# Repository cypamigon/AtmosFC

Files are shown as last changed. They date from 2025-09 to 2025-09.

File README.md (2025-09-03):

# AtmosFC

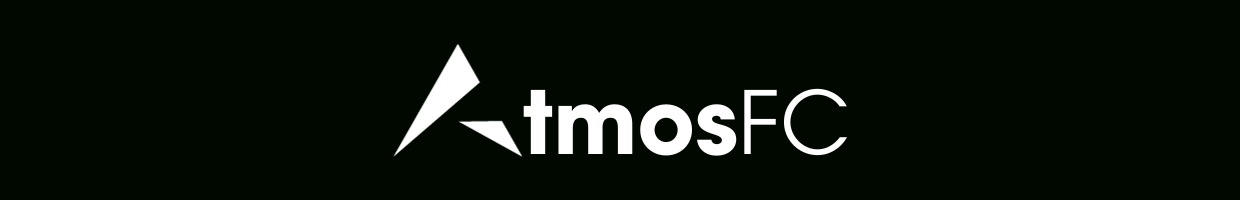
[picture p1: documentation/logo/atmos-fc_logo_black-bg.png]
AtmosFC Logo
 

AtmosFC is an open-hardware quadcopter flight controller designed in KiCad. Powered by an STM32G4 MCU, it integrates high-performance sensors and peripherals, and is fully compatible with Betaflight (≥ 4.5).

<p align="center"> AtmosFC PCB </p> 

## Table of Contents
- [Features](#features)
- [Input / Output](#input--output)
- [Hardware Architecture](#hardware-architecture)
- [Flashing Betaflight](#flashing-betaflight)
- [Notes](#notes)
- [Gallery](#gallery)
- [Repository Structure](#repository-structure)
- [License](#license)

## Features

- **MCU**: STM32G473CEU6
- **IMU**: ICM-468-P
- **Barometer**: DPS-386
- **OSD**: MAX7456 for analog on-screen display
- **Blackbox**: 32MB onboard flash memory for log recording
- **Power input**: Up to 6S
- **Power monitoring**: Battery voltage and current sensing
- **Status indicators**: Green, Blue, and Amber LEDs
- **Dimensions**: 40x40mm
- **Mounting holes**: 30.5×30.5 mm (M4 holes for silicone inserts with M3 screws)
- **Weight**: 8.2g

## Input / Output 

- **USB connector**: USB Type-C
- **Motor outputs**: x4
- **ESC**: Current sensing and telemetry
- **UARTs**: x3
- **I2C**: Yes
- **Video Input / Video Output with OSD** 
- **5V outputs**: up to 3A total 
- **Buzzer output**

## Hardware Architecture

The block diagram below shows the main hardware components and their interconnections.

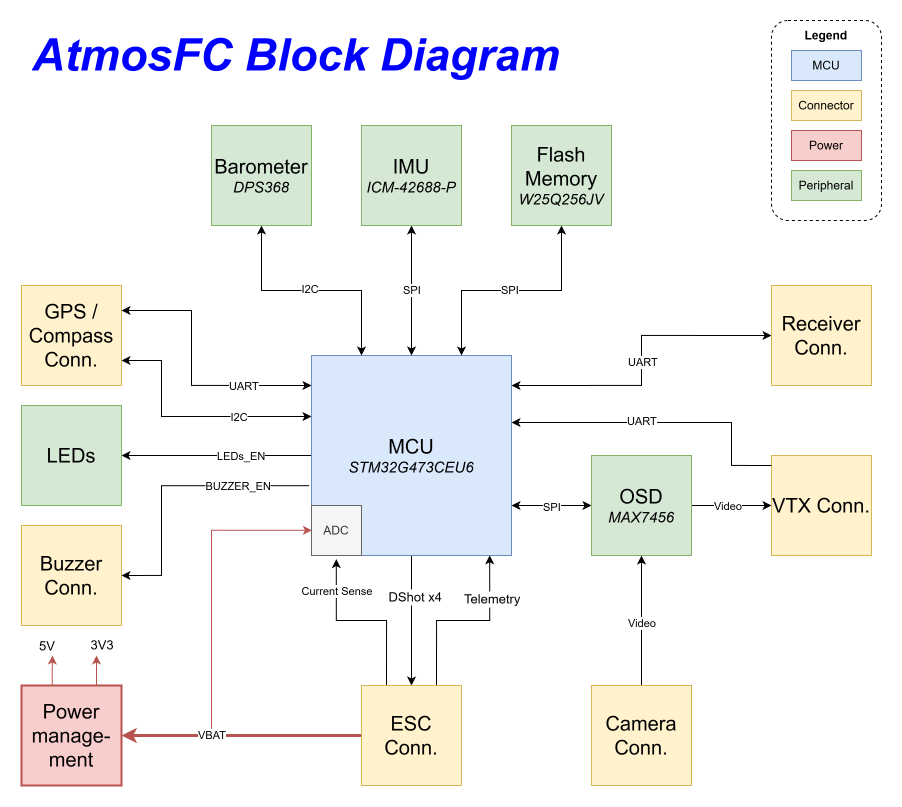
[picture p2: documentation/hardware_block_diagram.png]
AtmosFC Hardware Block Diagram
 

##  Flashing Betaflight

AtmosFC runs **Betaflight ≥ 4.5**. You can either flash the precompiled Betaflight 4.5 firmware or build the latest from source.

### Option 1 – Using the provided firmware
1. Open **Betaflight Configurator**.  
   If you don’t have it installed, get the latest version here : [Betaflight Configurator Releases](https://github.com/betaflight/betaflight-configurator/releases/latest)
3. Connect AtmosFC via USB-C.
4. If required, enter DFU mode (hold the BOOT button while plugging in USB).
5. In the Betaflight Configurator, go to **Firmware Flasher → Load firmware [Local]** and select the file `betaflight_4.5.0_ATMOSFC.hex` in `betaflight_config/`.
6. Click **Flash Firmware** and wait for the board to reboot.

### Option 2 – Building from Source

1. Clone the [Betaflight Repository](https://github.com/betaflight/betaflight) and install the required toolchain. Follow the official setup guide for your OS : [Betaflight Building Docs](https://betaflight.com/docs/category/building).
2. In the Betaflight root directory, update the target list by running:
```
> make configs
```
3. Add the AtmosFC board configuration by copying the folder `betaflight_config/ATMOSFC/` into `betaflight/src/config/configs`.
4. Build the firmware for AtmosFC target.
```
> make ATMOSFC
```
5. The compiled `.hex` file will be located under `betaflight/obj/`.
Flash it using **Betaflight Configurator** (follow the steps from Option 1).

## Notes 
- The board has been **successfully tested with Betaflight 4.5**. All basic functions, including motor outputs, sensors, LEDs, were working correctly.
- **I did not test the OSD feature**, as I was flying using digital FPV goggles instead of analog video.
- There is a small **voltage drop on the VBAT measurement** (~0.2-0.3V) due to the Schottky diode used for reverse polarity protection.  
  - This can be compensated either by applying a software offset in Betaflight, or by using an alternative reverse polarity protection method, such as a MOSFET-based circuit

## Gallery

<p align="center">
  
    <br>
  
    <br>
  
    <br>
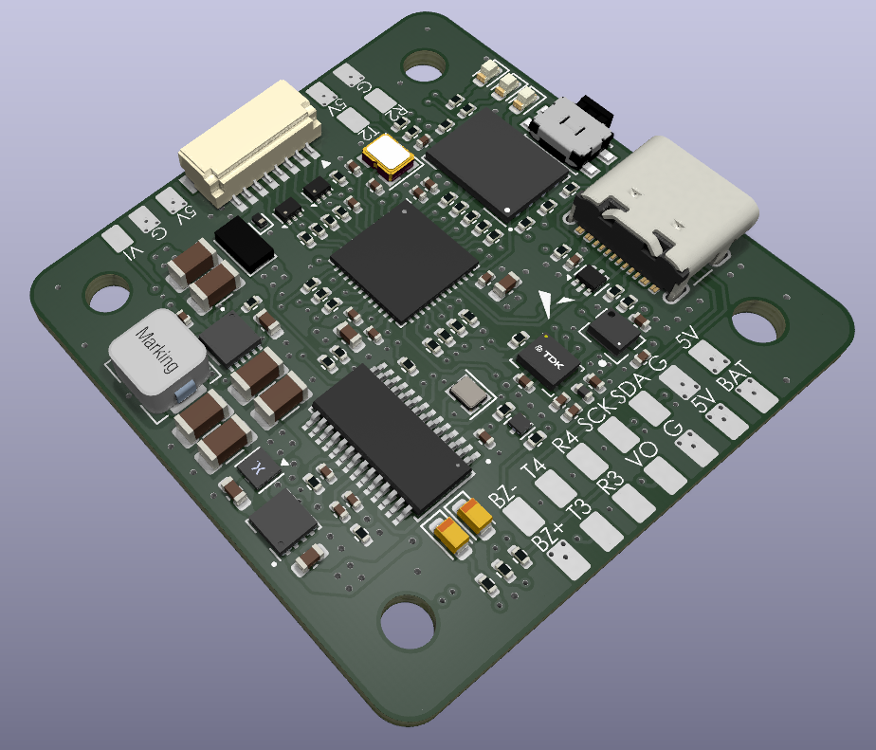
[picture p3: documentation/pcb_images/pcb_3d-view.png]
  
    <br>
  
</p>

## Repository Structure

The repository is organized as follows:

``` bash
├── hardware/             
│   ├── atmos_fc/           # KiCad project files (.kicad_pcb, .sch, etc.)  
│   ├── assembly/           # Fabrication files (Gerber, BOM)
│   └── lib/                # Custom footprints, symbols, 3D models
├── betaflight_config/
│   ├── ATMOSFC/            # Board configuration for Betaflight ≥ 4.5
│   └── betaflight_4.5.0_ATMOSFC.hex    # Precompiled Betaflight 4.5 firmware
├── documentation/          # Schematic (.pdf), images, logo, block diagram
└── README.md
```

##  License

This project is released under the **[MIT License](LICENSE.txt)**.  
You are free to use, modify, and distribute it.

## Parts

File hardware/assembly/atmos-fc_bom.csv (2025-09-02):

Reference | Value | Qty | Description | Manufacturer | Mfr Part Number
C19,C20 | 10p | 2 | Multilayer Ceramic Capacitors MLCC - SMD/SMT 10 pF 50 VDC 5% 0402 C0G (NP0) | Murata Electronics | GRM1555C1H100JA01D
C30 | 10n | 1 | Multilayer Ceramic Capacitors MLCC - SMD/SMT 0.01 uF 25 VDC 2% 0402 C0G (NP0) | Murata Electronics | GRM1555C1E103GE01D
C3,C12,C13,C14,C15,C16,C18,C21,C22,C23,C24,C29,C31,C32,C33,C34 | 100n | 16 | Multilayer Ceramic Capacitors MLCC - SMD/SMT 16V 0.1uF X7R 0402 10 % | TAIYO YUDEN | MSASE105SB7104KFNA01
C4 | 1u | 1 | Multilayer Ceramic Capacitors MLCC - SMD/SMT 25V 1uF X7R 0603 10 % | TAIYO YUDEN | MSAST168SB7105KTNA01
C1,C2 | 10u | 2 | Multilayer Ceramic Capacitors MLCC - SMD/SMT 35V 10uF X7R 1206 10 % | TAIYO YUDEN | MCJCG31LBB7106KTPA01
L1 | 10u | 1 | Power Inductors - SMD Ind,5.7x5.2x2.8mm,10uH+/-20%,2.8A,shd | Bourns | SRP5030CC-100M
C5,C6,C7,C8 | 22u | 4 | Multilayer Ceramic Capacitors MLCC - SMD/SMT 16V 22uF X7R 1206 20 % | TAIYO YUDEN | MSASE31LBB7226MTNA01
C25,C26 | 47u | 2 | Tantalum Capacitors - Solid SMD 10V 47uF 0805 Tol +/-20% | KYOCERA AVX | F981A476MSAAS1
R2,R3,R8,R9,R11,R12,R17,R20,R21,R27,R28,R29,R30,R31,R32,R33,R34,R35,R36,R37,R38 | 33R | 21 | Thick Film Resistors - SMD 1/16watt 33ohms 1% 100ppm | Vishay / Dale | CRCW040220K0FKED
R16,R19 | 75R | 2 | Thick Film Resistors - SMD 1/16watt 75ohms 1% | Vishay / Dale | CRCW040275R0FKED
R13 | 100R | 1 | Thick Film Resistors - SMD 1/16watt 100ohms 1% Commercial Use | Vishay / Dale | CRCW0402100RFKEDC
R15 | 130R | 1 | Thick Film Resistors - SMD 1/16watt 130ohms 1% Commercial Use | Vishay / Dale | CRCW0402130RFKEDC
R14 | 220R | 1 | Thick Film Resistors - SMD 1/16watt 220ohms 1% | Vishay / Dale | CRCW0402220RFKED
R39 | 1k | 1 | Thick Film Resistors - SMD 1/16watt 1.0Kohms 1% | Vishay / Dale | CRCW04021K00FKED
R7 | 4.7k | 1 | Thick Film Resistors - SMD 1/16watt 4.7Kohms 1% Commercial Use | Vishay / Dale | CRCW04024K70FKEDC
R4,R5,R10,R18 | 10k | 4 | Thick Film Resistors - SMD 1/16watt 10Kohms 1% Commercial Use | Vishay / Dale | CRCW040210K0FKEDC
R1 | 20k | 1 | Thick Film Resistors - SMD 1/16watt 20Kohms 1% | Vishay / Dale | CRCW040220K0FKED
R6,R22,R23,R24 | 47k | 4 | Thick Film Resistors - SMD 1/16watt 47Kohms 1% Commercial Use | Vishay / Dale | CRCW040247K0FKEDC
Y1 | 8MHz | 1 | Crystals 8MHz 10 pF 3225 TOL +/-10, STAB +/-30 ppm, -40 +85 C, 400O | ECS | ECS-80-10-33-CGN-TR3
Y2 | 27MHz | 1 | Crystals 27MHz 8pF AEC-Q200 2 .05X1.65X.45mm | KYOCERA AVX | CX2016SA27000D0GSSCC
FB1 | 120R@100MHz | 1 | Ferrite Beads 0402 120ohm 25% 5A AEC-Q200 | Murata Electronics | BLM15PX121BH1D
C27,C28 | 2u2 | 2 | Multilayer Ceramic Capacitors MLCC - SMD/SMT 2.2 uF 10 VDC 10% 0402 X7S | Murata Electronics | GRM155C71A225KE11D
C9,C10,C11,C17 | 4u7 | 4 | Multilayer Ceramic Capacitors MLCC - SMD/SMT 4.7 uF 16 VDC 10% 0603 X7R | Murata Electronics | GRM188Z71C475KE21J
R25,R26 | 5k1 | 2 | Thick Film Resistors - SMD 1/16watt 5.1Kohms 1% | Vishay / Dale | CRCW04025K10FKED
Q1 | BC817 | 1 | Bipolar Transistors - BJT SOT8015 45V .5A NPN GP TRANS | Nexperia | BC817-40QBH-QZ
D2 | D_Schottky | 1 | Schottky Diodes & Rectifiers 7A, 100V, DFN3820A TRENCH SKY RECT. | Vishay Semiconductors | V7N103HM3/I
D1 | D_TVS | 1 | ESD Protection Diodes / TVS Diodes ESD 30V BI | Nexperia | PESD30VF1BBL-QYL
R40 | DNP | 1
U7 | DPS368XTSA1 | 1 | Digital XENSIVTM barometric pressure sensor | Infineon Technologies | DPS368XTSA1
U5 | ICM-42688-P | 1 | High Precision 6-Axis MEMS MotionTrackingTM Device | TDK InvenSense | ICM-42688-P
J2 | JST-SH 8p | 1 | Headers & Wire Housings SR HEADER (SMT SIDE) | JST Sales America Inc. | SM08B-SRSS-TB
U4 | MAX7456 | 1 | Single-Channel Monochrome On-Screen Display with Integrated EEPROM | Analog Devices | MAX7456EUI+
U1 | MAX25232 | 1 | 36V, 3A Mini Buck Converters with 3.5uA IQ | Analog Devices | MAX25232ATCD_V+
D3 | PMEG2020CPASX | 1 | Schottky Diodes & Rectifiers RECTIFIER SOT1061/HUSON3 | Nexperia | PMEG2020CPASX
D7,D8 | SP1001-04XTG | 2 | 8pF 15kV Unidirectional TVS Array | Littlefuse | SP1001-04XTG
U3 | STM32G473CEU6 | 1 | ARM Microcontrollers - MCU Mainstream Arm Cortex-M4 MCU 170MHz 512Kbytes of Flash Math Accel, High Analog | STMicroelectronics | STM32G473CEU6
SW1 | SW_Push | 1 | Tactile Switches Tact Switch SMT 1.65mm | Wurth Elektronik | 436331045822
U2 | TPS78533BQDRBRQ1 | 1 | TPS785-Q1 Automotive, 1-A, High-PSRR Low-Dropout Voltage Regulator With High Accuracy and Enable | Texas Instruments | TPS78533BQWDRBRQ1
J3 | USB_C_Receptacle_USB2.0_16P | 1 | USB 2.0-only 16P Type-C Receptacle connector | GCT | USB4105-GF-A
U8 | USBLC6-2P6 | 1 | Very low capacitance ESD protection diode, 2 data-line, SOT-666 | STMicroelectronics | USBLC6-2P6
U6 | W25Q256JVE | 1 | 3V 256M-BIT SERIAL FLASH MEMORY WITH DUAL/QUAD SPI | Winbond | W25Q256JVEIQ
D4,D5,D6 | ~ | 3 | -- valeurs mixtées -- | ams OSRAM | -- valeurs mixtées --

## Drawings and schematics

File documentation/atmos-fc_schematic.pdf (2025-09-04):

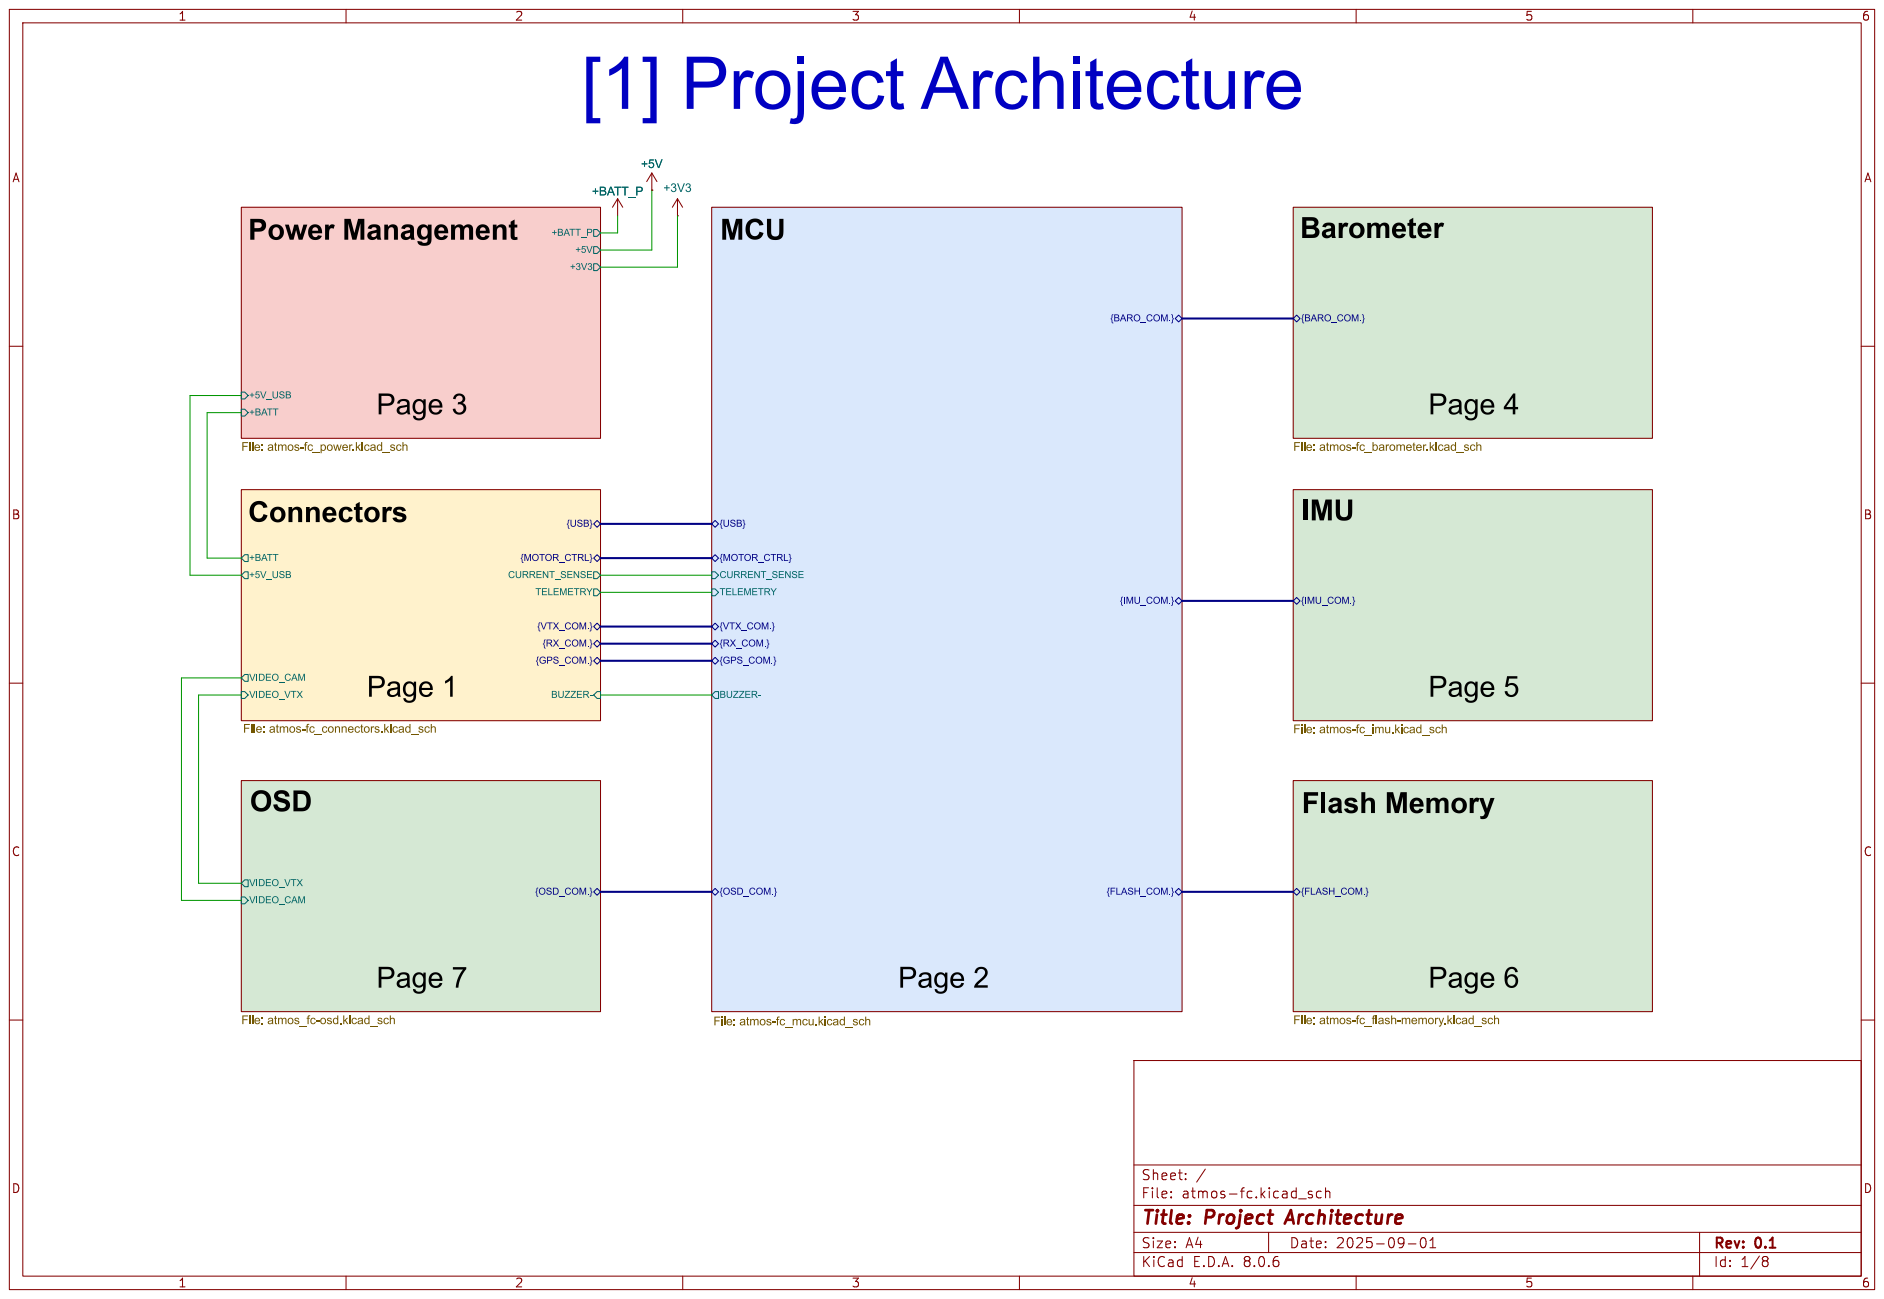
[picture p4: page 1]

+5V_USB Power Management +BATT_P File: atmos-fc_power.kicad_sch

File: atmos-fc.kicad_sch Sheet: / VIDEO_CAM

Id: 1/8 Title: Project Architecture

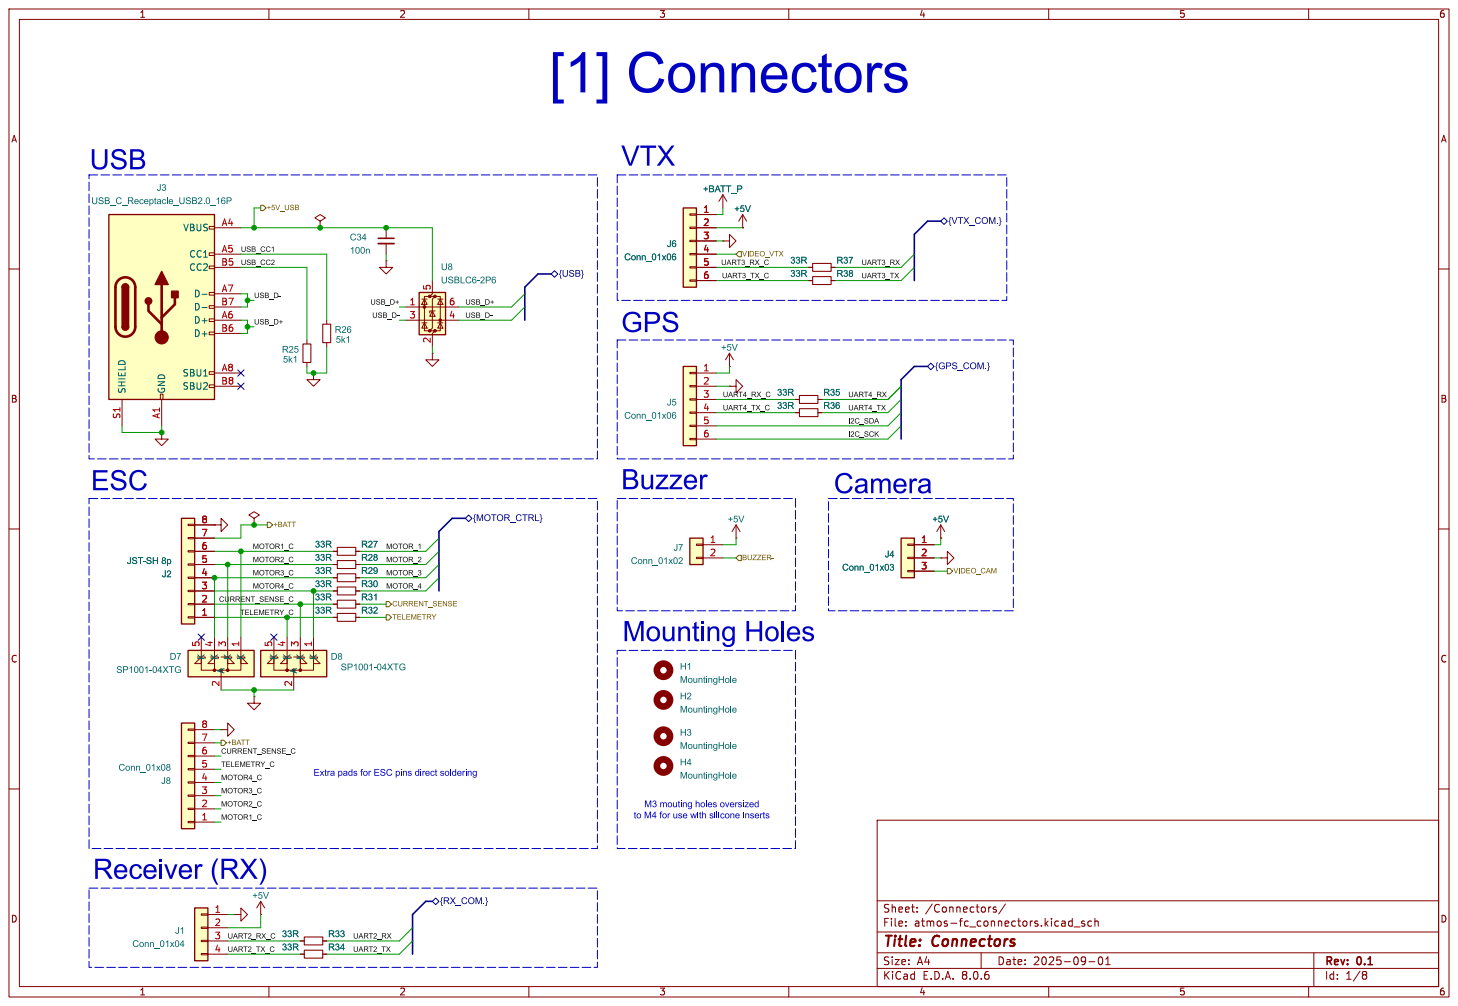
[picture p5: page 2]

4 4
3 3
2 2
1 1 | TELEMETRY_C

File: atmos-fc_connectors.kicad_sch Sheet: /Connectors/ H2 MountingHole H3 MountingHole +5V

Extra pads for ESC pins direct soldering

to M4 for use with silicone inserts Receiver (RX)

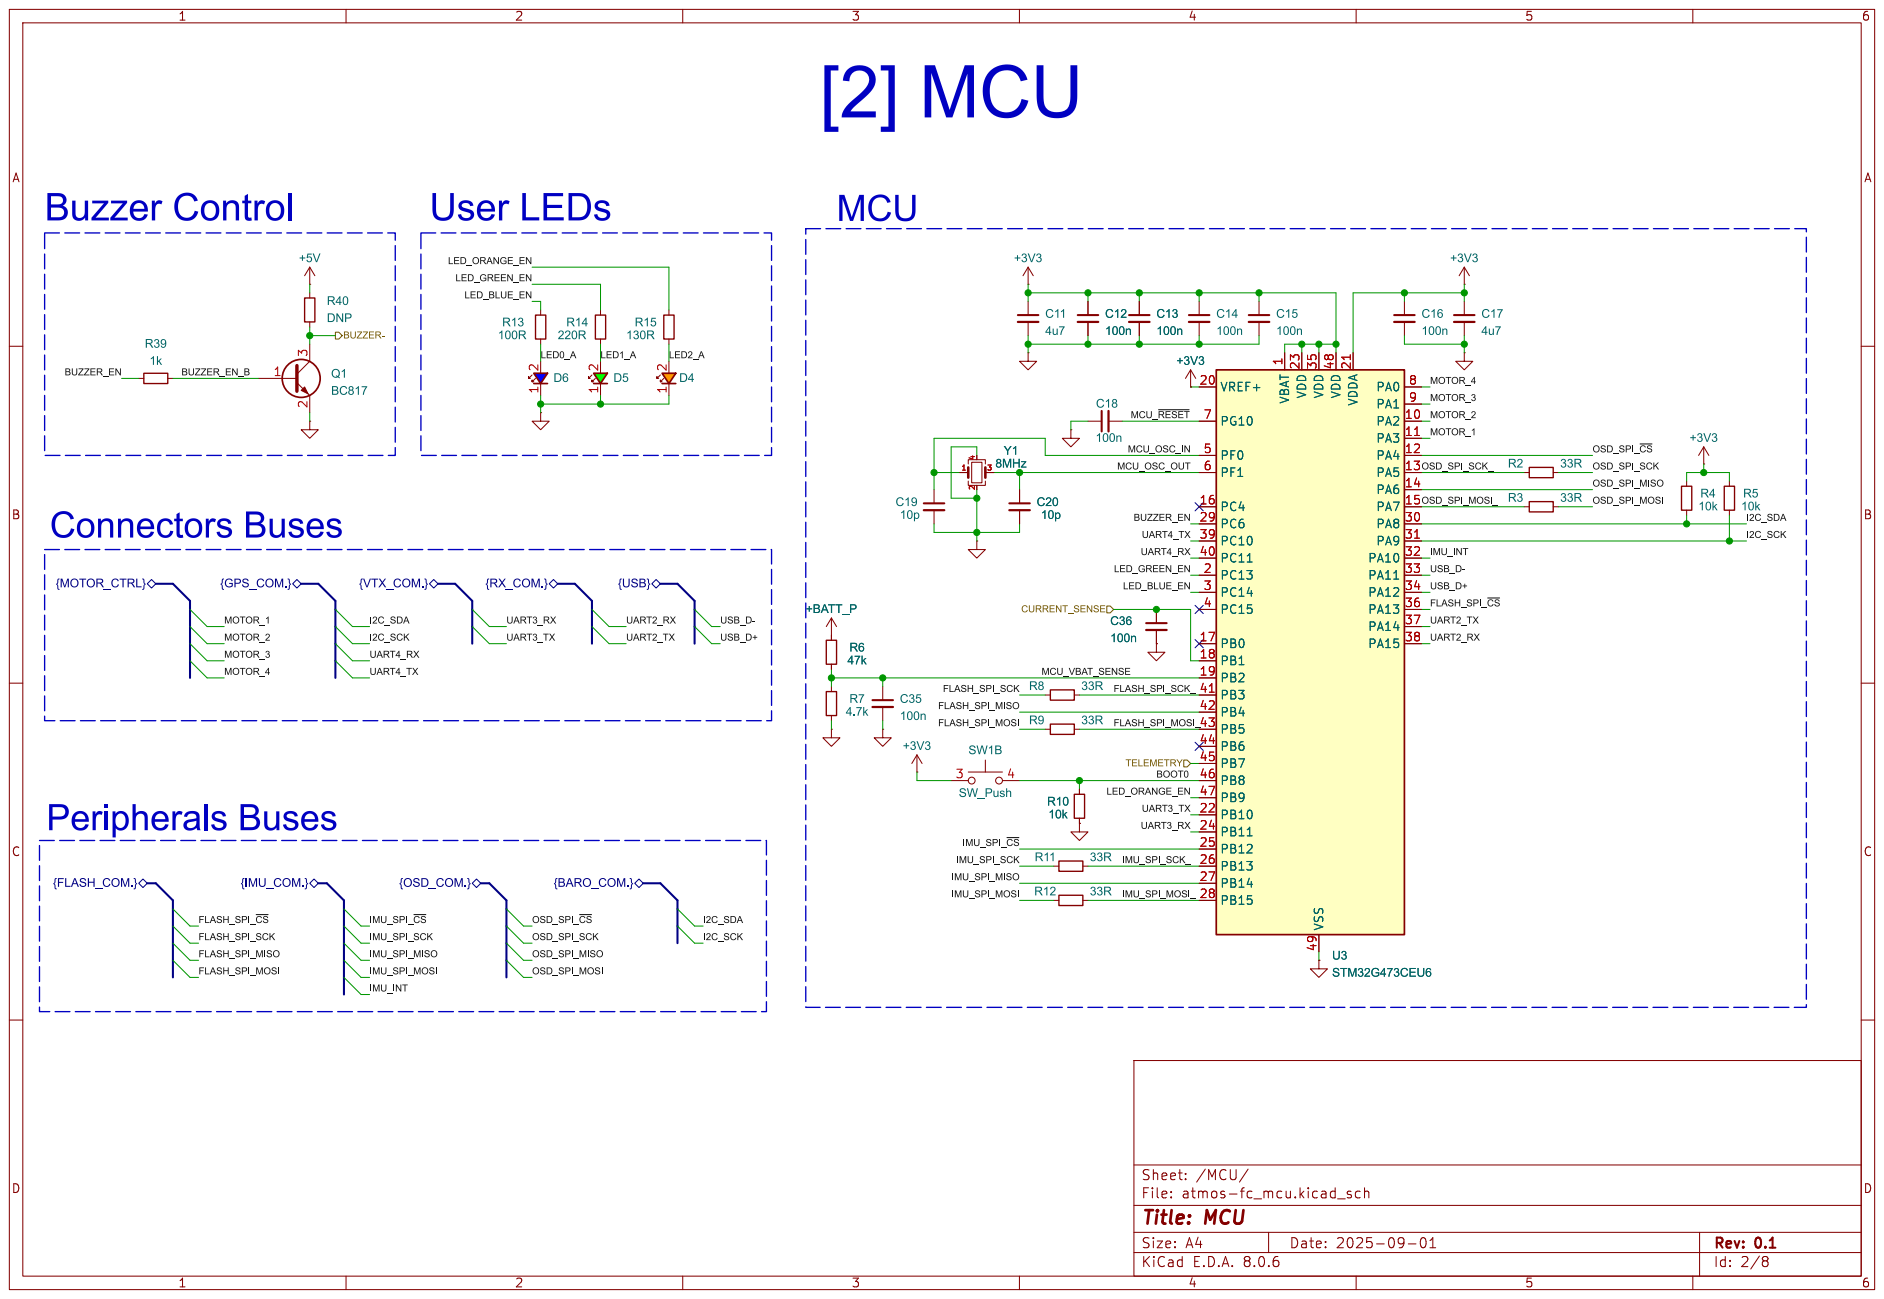
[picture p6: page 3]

1 PA2 10 PA3 11 PA4 12 PA5 13 PA6 14 PA7 15 PC4 16 PB0 17 PB1 18 PB2 19 PC13 2 VREF+ 20 VDDA 21 PB10 22 VDD 23 PB11 24 PB12 25 PB13 26 PB14 27 PB15 28 PC6 29 PC14 3 PA8 30 PA9 31 PA10 32 PA11 33 PA12 34 VDD 35 PA13 36 PA14 37 PA15 38 PC10 39 PC15 4 PC11 40 PB3 41 PB4 42 PB5 43 PB6 44 PB7 45 PB8 46 PB9 47 VDD 48 VSS 49 PF0 5 PF1 6 PG10 7 PA0 8 PA1 9 +BATT_PR6

1 PA2 10 PA3 11 PA4 12 PA5 13 PA6 14 PA7 15 PC4 16 PB0 17 PB1 18 PB2 19 PC13 2 VREF+ 20 VDDA 21 PB10 22 VDD 23 PB11 24 PB12 25 PB13 26 PB14 27 PB15 28 PC6 29 PC14 3 PA8 30 PA9 31 PA10 32 PA11 33 PA12 34 VDD 35 PA13 36 PA14 37 PA15 38 PC10 39 PC15 4 PC11 40 PB3 41 PB4 42 PB5 43 PB6 44 PB7 45 PB8 46 PB9 47 VDD 48 VSS 49 PF0 5 PF1 6 PG10 7 PA0 8 PA1 9 U3STM32G473CEU6

File: atmos-fc_mcu.kicad_sch Sheet: /MCU/
Id: 2/8 Title: MCU

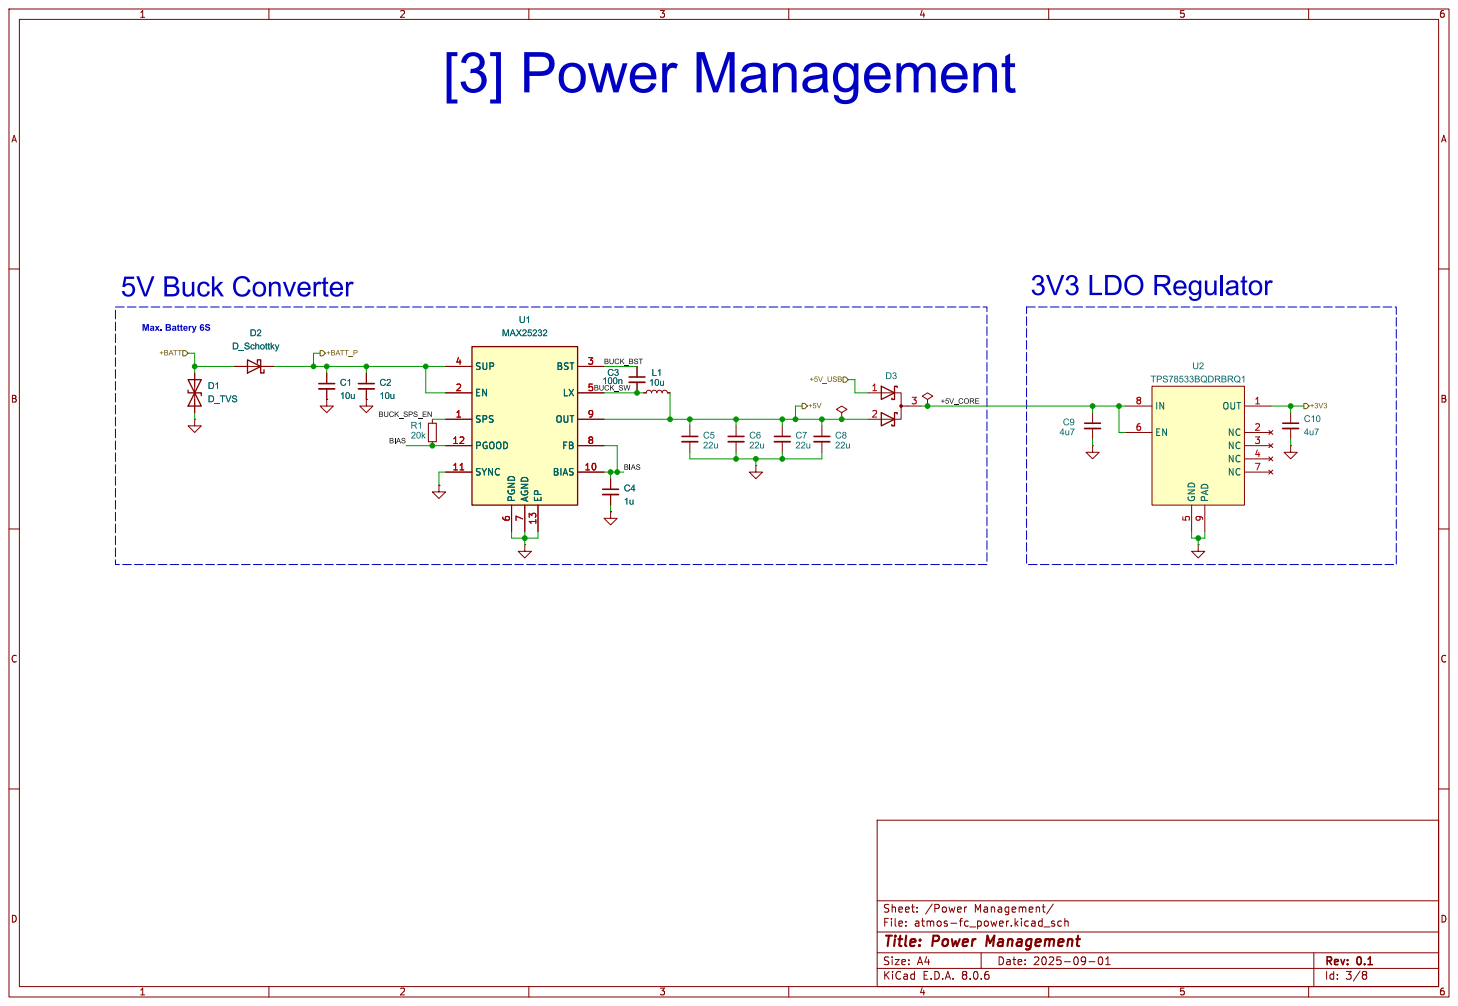
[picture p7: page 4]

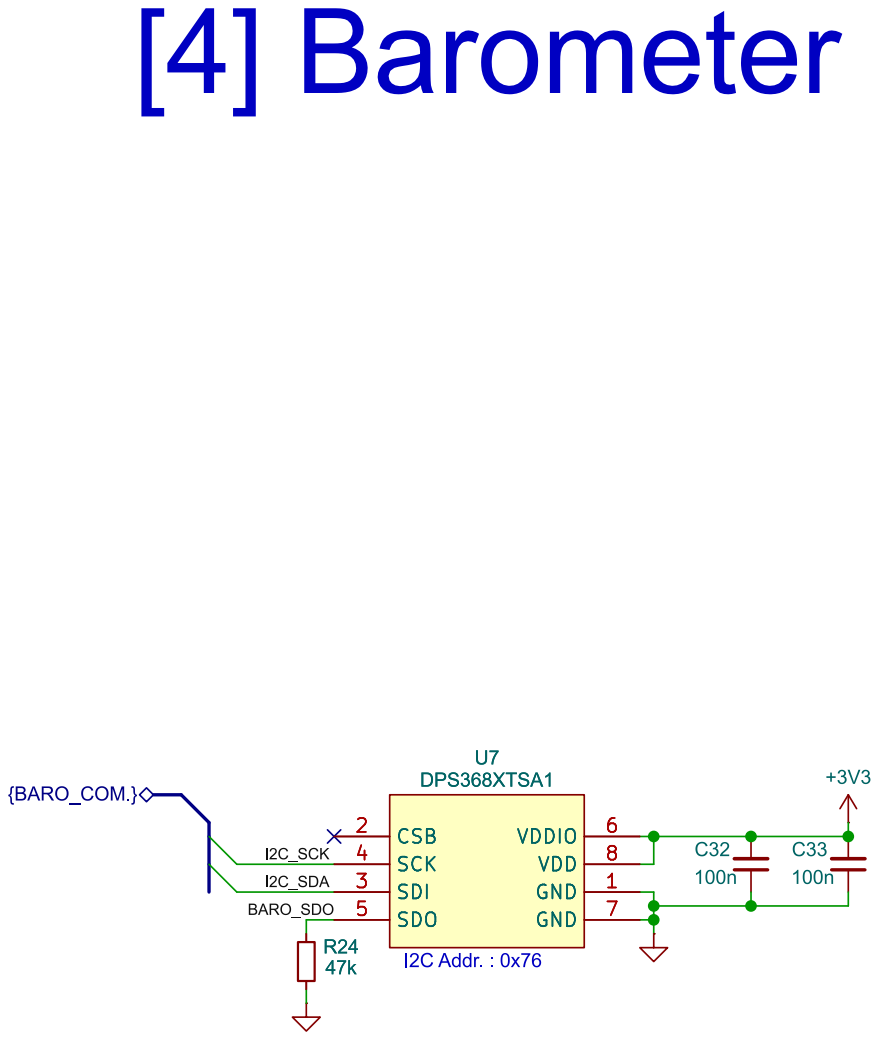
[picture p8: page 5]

Id: 4/8 Title: Barometer File: atmos-fc_barometer.kicad_sch Sheet: /Barometer/

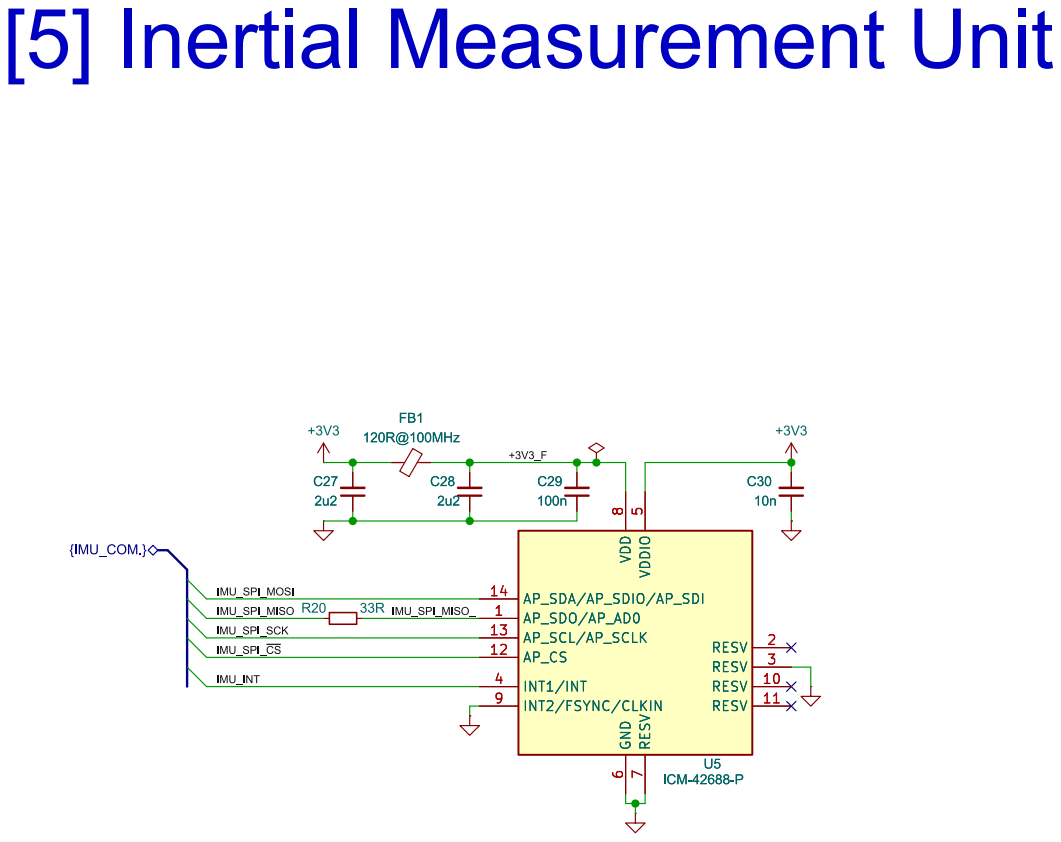
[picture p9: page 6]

Id: 5/8 Title: Inertial Measurement Unit File: atmos-fc_imu.kicad_sch Sheet: /IMU/

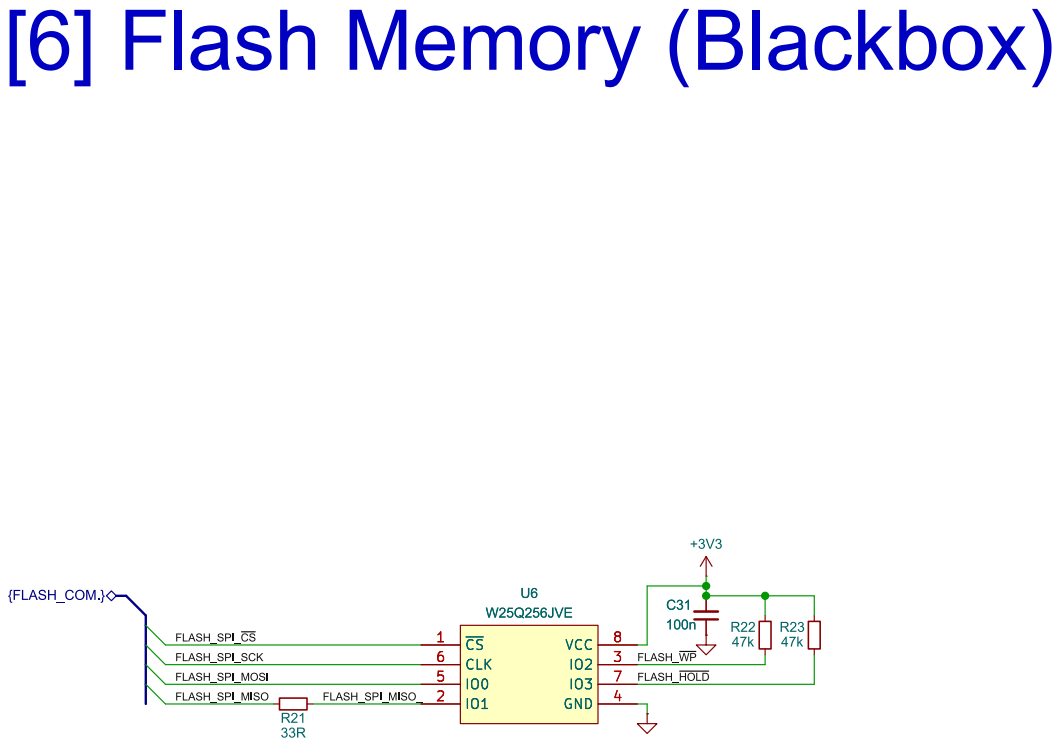
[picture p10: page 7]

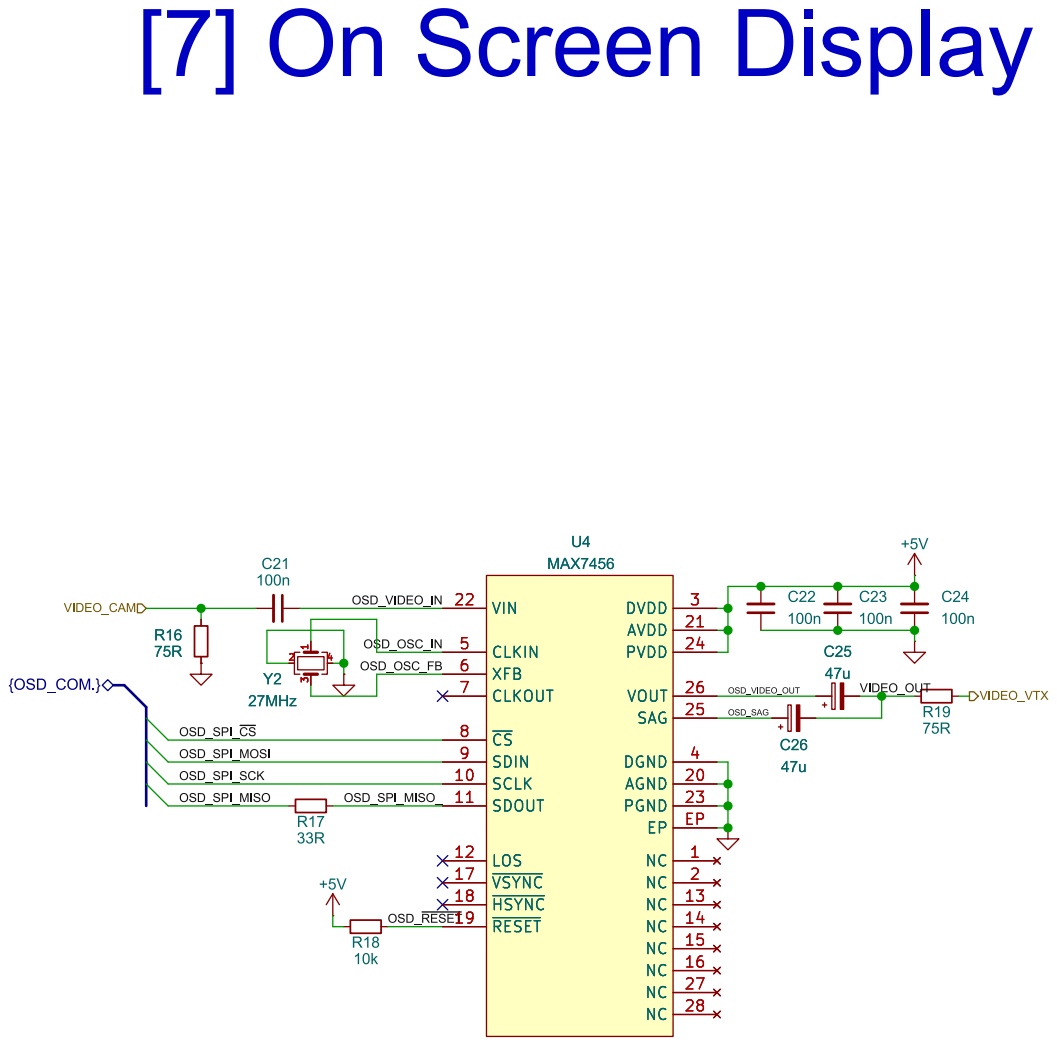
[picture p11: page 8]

OSD_VIDEO_OUT OSD_OSC_FB OSD_SPI_MISO_ OSD_VIDEO_IN OSD_OSC_IN OSD_~{RESET} [7] On Screen Display

File: atmos_fc-osd.kicad_sch Sheet: /OSD/
Id: 7/8 Title: On Screen Display

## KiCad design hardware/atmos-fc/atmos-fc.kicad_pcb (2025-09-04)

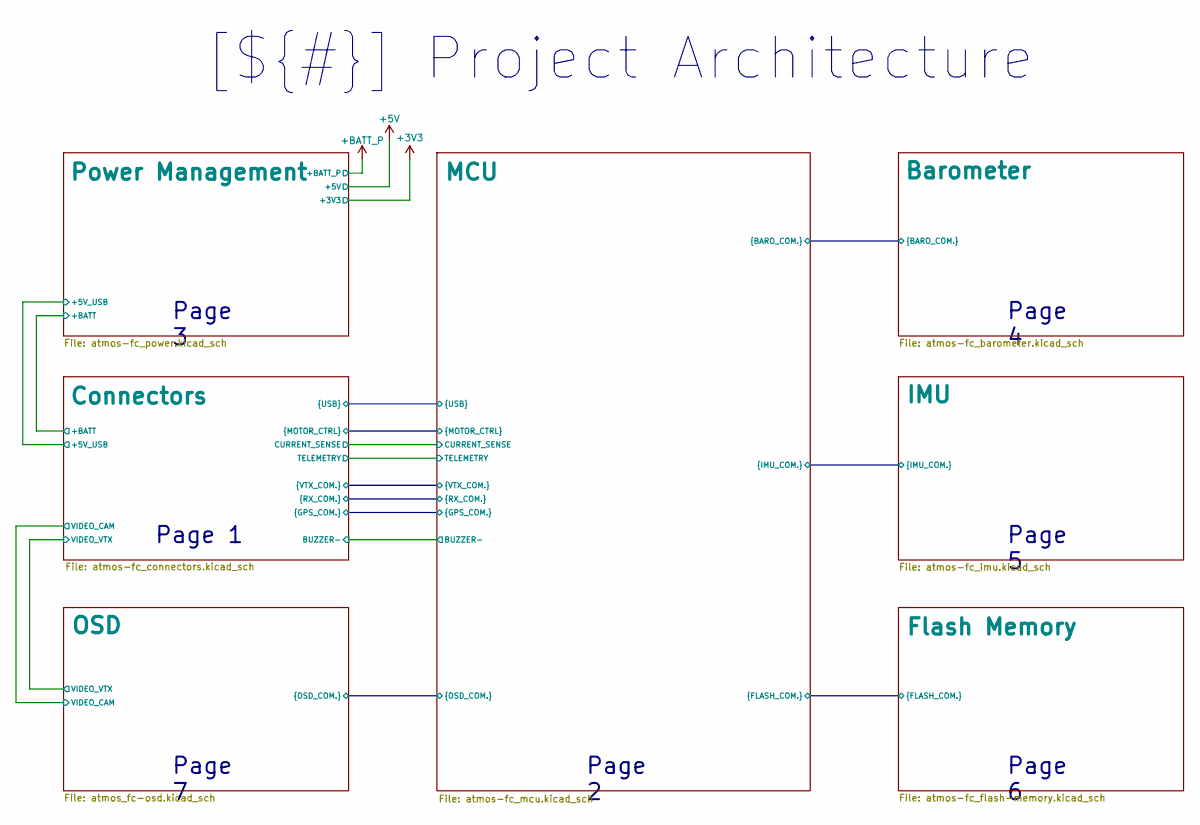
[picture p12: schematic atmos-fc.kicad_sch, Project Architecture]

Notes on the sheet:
Page 3
Page 6
Page 4
[${#}] ${TITLE}
Page 5
Page 2
Page 1
Page 7

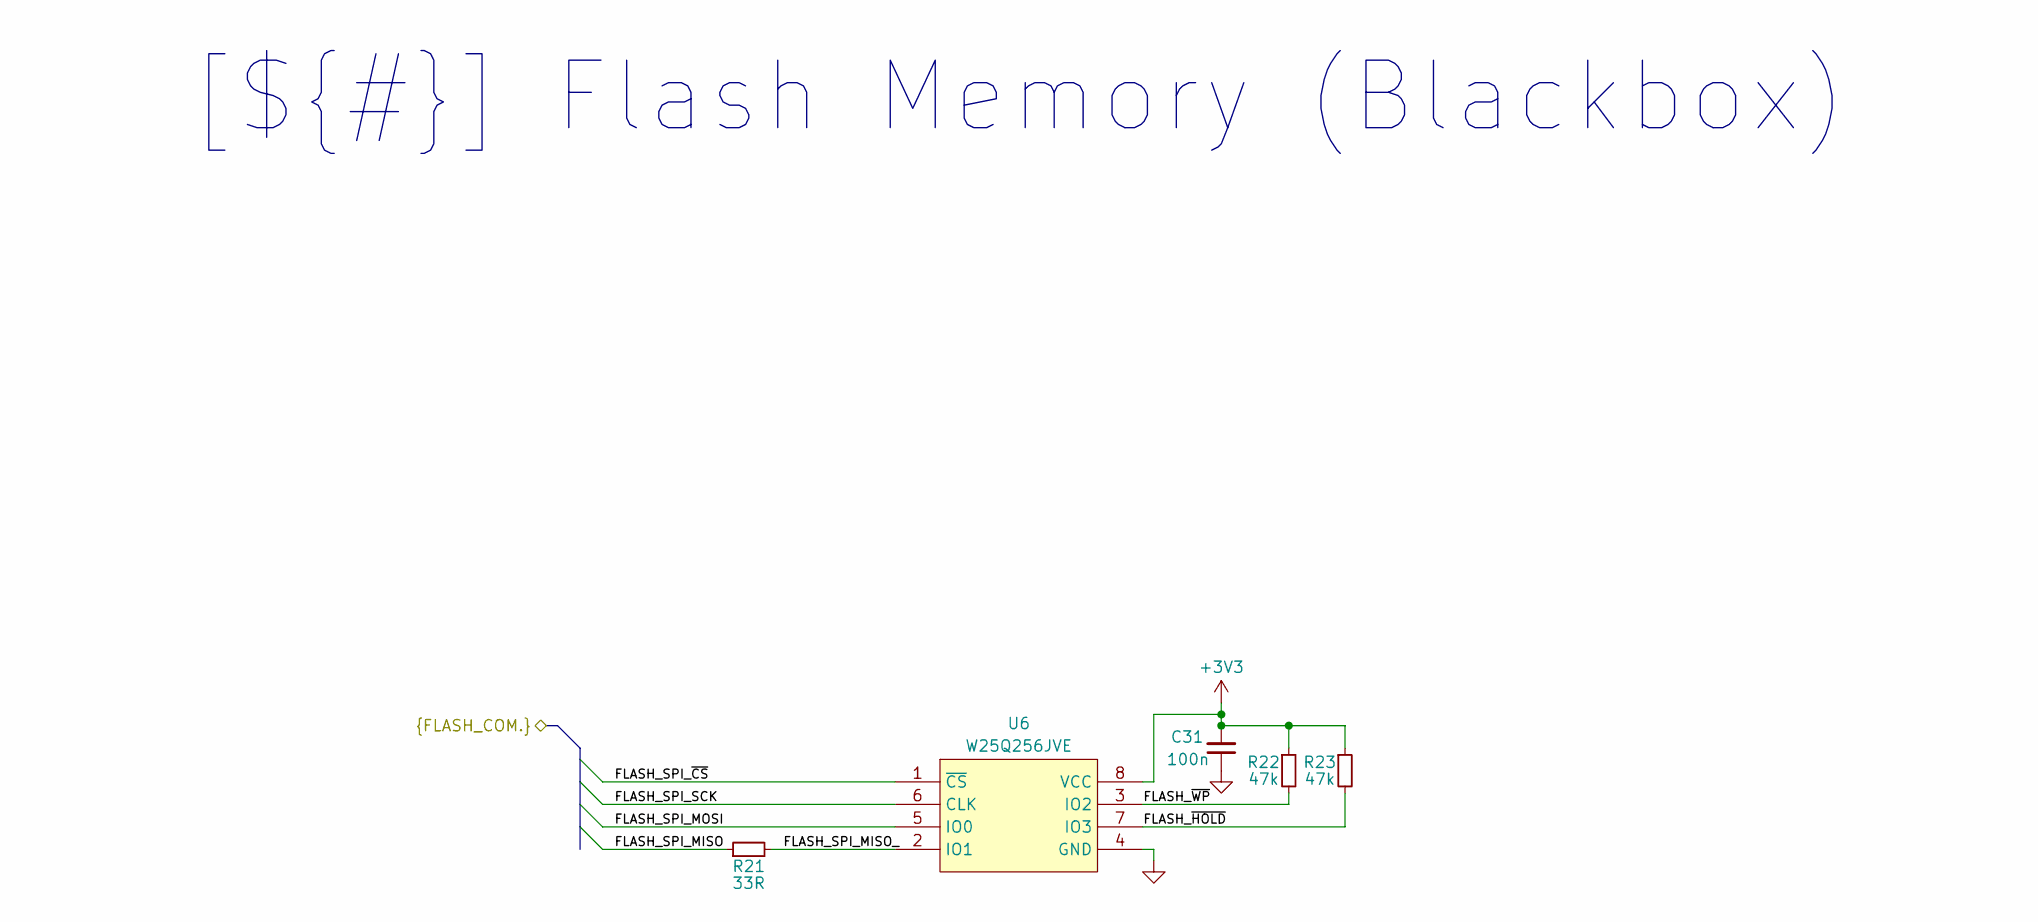
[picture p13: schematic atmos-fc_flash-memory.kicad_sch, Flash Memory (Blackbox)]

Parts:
C31: 100n; C_0402_1005Metric; Mfr Part Number MSASE105SB7104KFNA01
R21: 33R; R_0402_1005Metric; Mfr Part Number CRCW040220K0FKED
R22, R23: 47k; R_0402_1005Metric; Mfr Part Number CRCW040247K0FKEDC
U6: W25Q256JVE; WSON-8-1EP_8x6mm_P1.27mm; Mfr Part Number W25Q256JVEIQ

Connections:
+3V3: C31.2, R22.1, R23.1, U6.8 (VCC); also elsewhere on the board
/Flash Memory/FLASH_SPI_MISO: R21.1; also elsewhere on the board
/Flash Memory/FLASH_SPI_MISO_: R21.2, U6.2 (IO1)
/Flash Memory/FLASH_SPI_MOSI: U6.5 (IO0); also elsewhere on the board
/Flash Memory/FLASH_SPI_SCK: U6.6 (CLK); also elsewhere on the board
/Flash Memory/FLASH_SPI_~CS: U6.1 (~CS); also elsewhere on the board
/Flash Memory/FLASH_~HOLD: R23.2, U6.7 (IO3)
/Flash Memory/FLASH_~WP: R22.2, U6.3 (IO2)
GND: C31.1, U6.4 (GND); also elsewhere on the board

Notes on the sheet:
[${#}] ${TITLE}

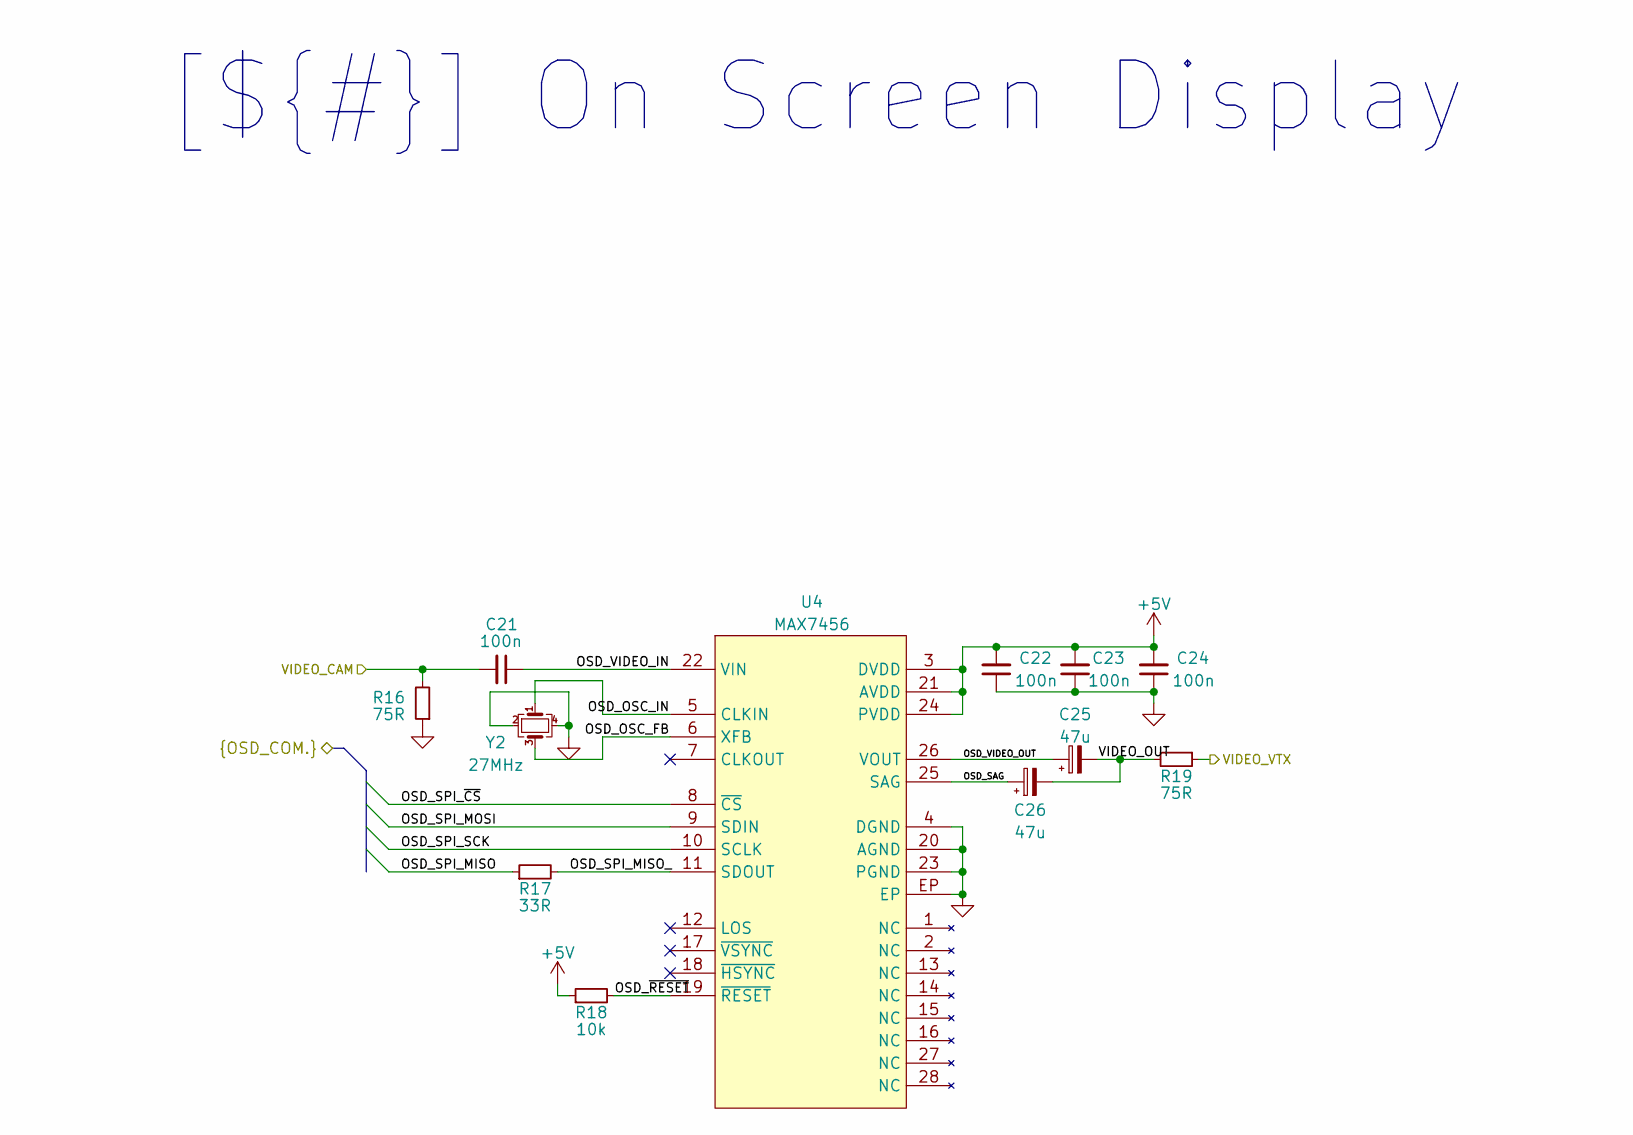
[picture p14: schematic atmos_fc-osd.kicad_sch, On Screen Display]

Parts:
C21, C22, C23, C24: 100n; C_0402_1005Metric; Mfr Part Number MSASE105SB7104KFNA01
C25, C26: 47u; CP_EIA-2012-12_Kemet-R; Mfr Part Number F981A476MSAAS1
R16, R19: 75R; R_0402_1005Metric; Mfr Part Number CRCW040275R0FKED
R17: 33R; R_0402_1005Metric; Mfr Part Number CRCW040220K0FKED
R18: 10k; R_0402_1005Metric; Mfr Part Number CRCW040210K0FKEDC
U4: MAX7456; TSSOP-28-1EP_4.4x9.7mm_P0.65mm_EP3.1x6.9mm; Mfr Part Number MAX7456EUI+
Y2: 27MHz; Crystal_SMD_2016-4Pin_2.0x1.6mm; Mfr Part Number CX2016SA27000D0GSSCC

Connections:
+5V: C22.2, C23.2, C24.2, R18.1, U4.3 (DVDD), U4.21 (AVDD), U4.24 (PVDD); also elsewhere on the board
/Connectors/VIDEO_CAM: C21.2, R16.2; also elsewhere on the board
/Connectors/VIDEO_VTX: R19.1; also elsewhere on the board
/MCU/OSD_SPI_MISO: R17.1; also elsewhere on the board
/MCU/OSD_SPI_MOSI: U4.9 (SDIN); also elsewhere on the board
/MCU/OSD_SPI_SCK: U4.10 (SCLK); also elsewhere on the board
/MCU/OSD_SPI_~CS: U4.8 (~CS); also elsewhere on the board
/OSD/OSD_OSC_FB: U4.6 (XFB), Y2.3
/OSD/OSD_OSC_IN: U4.5 (CLKIN), Y2.1
/OSD/OSD_SAG: C26.1, U4.25 (SAG)
/OSD/OSD_SPI_MISO_: R17.2, U4.11 (SDOUT)
/OSD/OSD_VIDEO_IN: C21.1, U4.22 (VIN)
/OSD/OSD_VIDEO_OUT: C25.1, U4.26 (VOUT)
/OSD/OSD_~RESET: R18.2, U4.19 (~RESET)
/OSD/VIDEO_OUT: C25.2, C26.2, R19.2
GND: C22.1, C23.1, C24.1, R16.1, U4.4 (DGND), U4.20 (AGND), U4.23 (PGND), U4.EP, Y2.2, Y2.4; also elsewhere on the board

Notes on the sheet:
[${#}] ${TITLE}

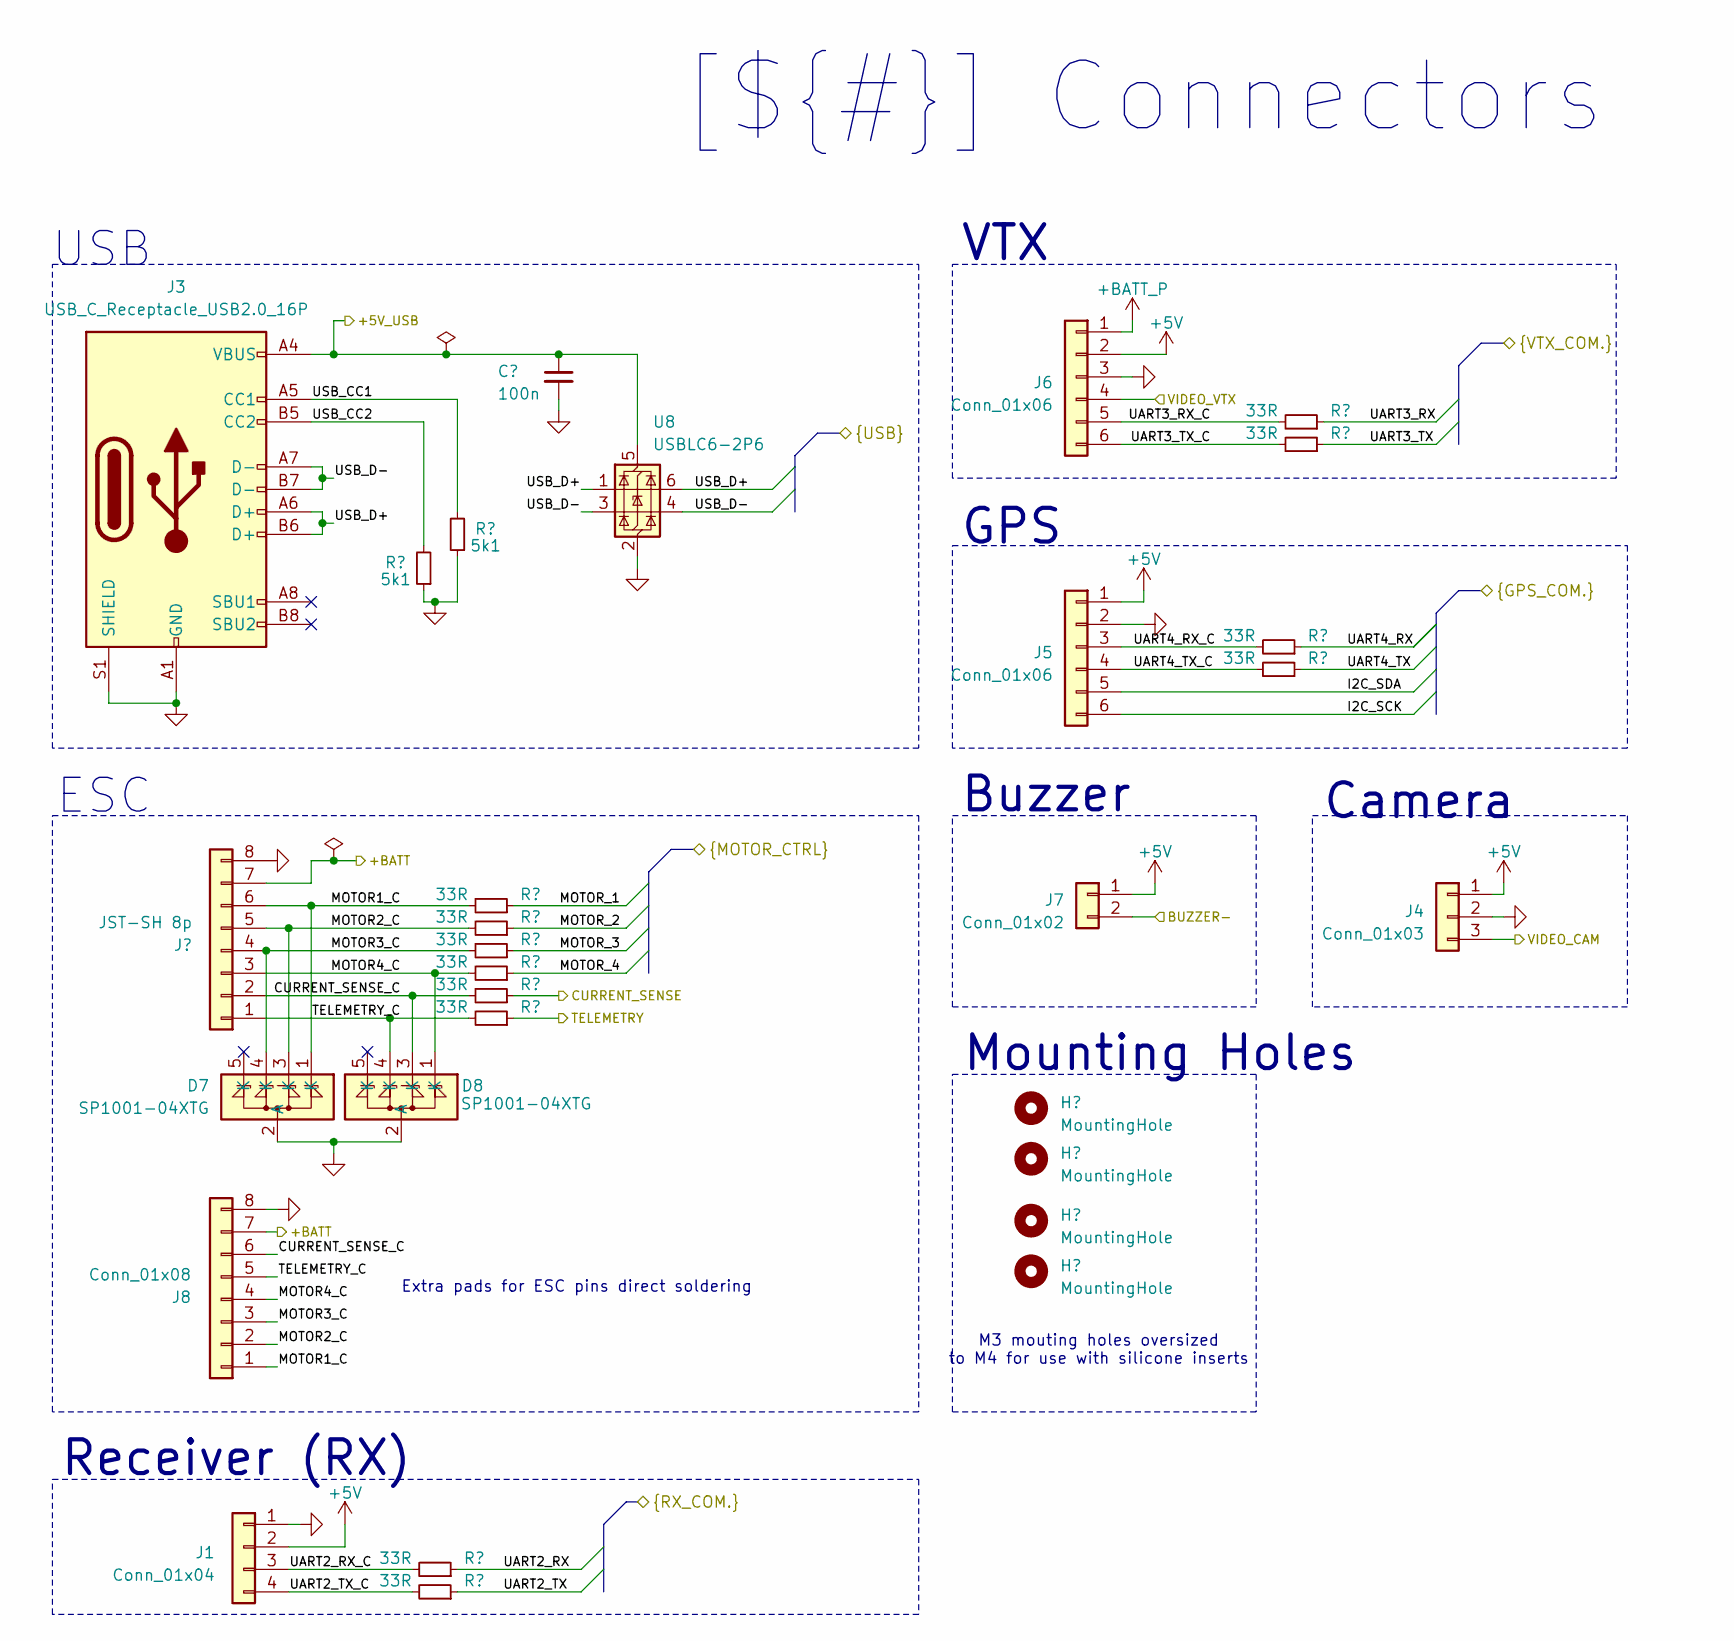
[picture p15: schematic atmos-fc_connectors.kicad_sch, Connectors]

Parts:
C34: 100n; C_0402_1005Metric; Mfr Part Number MSASE105SB7104KFNA01
D7, D8: SP1001-04XTG; SOT-553; Mfr Part Number SP1001-04XTG
H1, H2, H3, H4: MountingHole; MountingHole_4.3mm_M4
J1: Conn_01x04; SolderWirePads-2x2
J2: JST-SH 8p; JST_SR_SM08B-SRSS-TB; Mfr Part Number SM08B-SRSS-TB
J3: USB_C_Receptacle_USB2.0_16P; USB_C_Receptacle_GCT_USB4105-xx-A_16P_TopMnt_Horizontal; Mfr Part Number USB4105-GF-A
J4: Conn_01x03; SolderWirePads-1x3
J5, J6: Conn_01x06; SolderWirePads-1x6
J7: Conn_01x02; SolderWirePads-2x1
J8: Conn_01x08; SolderWirePads-2x4
R25, R26: 5k1; R_0402_1005Metric; Mfr Part Number CRCW04025K10FKED
R27, R28, R29, R30, R31, R32, R33, R34, R35, R36, R37, R38: 33R; R_0402_1005Metric; Mfr Part Number CRCW040220K0FKED
U8: USBLC6-2P6; SOT-666; Mfr Part Number USBLC6-2P6

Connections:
+5V: J1.2, J4.1, J5.1, J6.2, J7.1; also elsewhere on the board
+BATT_P: J6.1; also elsewhere on the board
/Connectors/+5V_USB: C34.1, J3.A4 (VBUS), J3.A9 (VBUS), J3.B4 (VBUS), J3.B9 (VBUS), U8.5 (VBUS); also elsewhere on the board
/Connectors/+BATT: J2.7, J8.7; also elsewhere on the board
/Connectors/BUZZER-: J7.2; also elsewhere on the board
/Connectors/CURRENT_SENSE: R31.1; also elsewhere on the board
/Connectors/CURRENT_SENSE_C: D8.3 (K), J2.2, J8.6, R31.2
/Connectors/I2C_SCK: J5.6; also elsewhere on the board
/Connectors/I2C_SDA: J5.5; also elsewhere on the board
/Connectors/MOTOR1_C: D7.1 (K), J2.6, J8.1, R27.2
/Connectors/MOTOR2_C: D7.3 (K), J2.5, J8.2, R28.2
/Connectors/MOTOR3_C: D7.4 (K), J2.4, J8.3, R29.2
/Connectors/MOTOR4_C: D8.1 (K), J2.3, J8.4, R30.2
/Connectors/MOTOR_1: R27.1; also elsewhere on the board
/Connectors/MOTOR_2: R28.1; also elsewhere on the board
/Connectors/MOTOR_3: R29.1; also elsewhere on the board
/Connectors/MOTOR_4: R30.1; also elsewhere on the board
/Connectors/TELEMETRY: R32.1; also elsewhere on the board
/Connectors/TELEMETRY_C: D8.4 (K), J2.1, J8.5, R32.2
/Connectors/UART2_RX: R33.1; also elsewhere on the board
/Connectors/UART2_RX_C: J1.3, R33.2
/Connectors/UART2_TX: R34.1; also elsewhere on the board
/Connectors/UART2_TX_C: J1.4, R34.2
/Connectors/UART3_RX: R37.1; also elsewhere on the board
/Connectors/UART3_RX_C: J6.5, R37.2
/Connectors/UART3_TX: R38.1; also elsewhere on the board
/Connectors/UART3_TX_C: J6.6, R38.2
/Connectors/UART4_RX: R35.1; also elsewhere on the board
/Connectors/UART4_RX_C: J5.3, R35.2
/Connectors/UART4_TX: R36.1; also elsewhere on the board
/Connectors/UART4_TX_C: J5.4, R36.2
/Connectors/USB_CC1: J3.A5 (CC1), R26.2
/Connectors/USB_CC2: J3.B5 (CC2), R25.2
/Connectors/USB_D+: J3.A6 (D+), J3.B6 (D+), U8.1 (I/O1), U8.6 (I/O1); also elsewhere on the board
/Connectors/USB_D-: J3.A7 (D-), J3.B7 (D-), U8.3 (I/O2), U8.4 (I/O2); also elsewhere on the board
/Connectors/VIDEO_CAM: J4.3; also elsewhere on the board
/Connectors/VIDEO_VTX: J6.4; also elsewhere on the board
GND: C34.2, D7.2 (A), D8.2 (A), J1.1, J2.8, J3.A1 (GND), J3.A12 (GND), J3.B1 (GND), J3.B12 (GND), J3.S1 (SHIELD), J4.2, J5.2, J6.3, J8.8, R25.1, R26.1, U8.2 (GND); also elsewhere on the board

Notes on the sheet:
[${#}] ${TITLE}
Camera
M3 mouting holes oversized to M4 for use with silicone inserts
Mounting Holes
Receiver (RX)
ESC
Buzzer
VTX
Extra pads for ESC pins direct soldering
GPS
USB

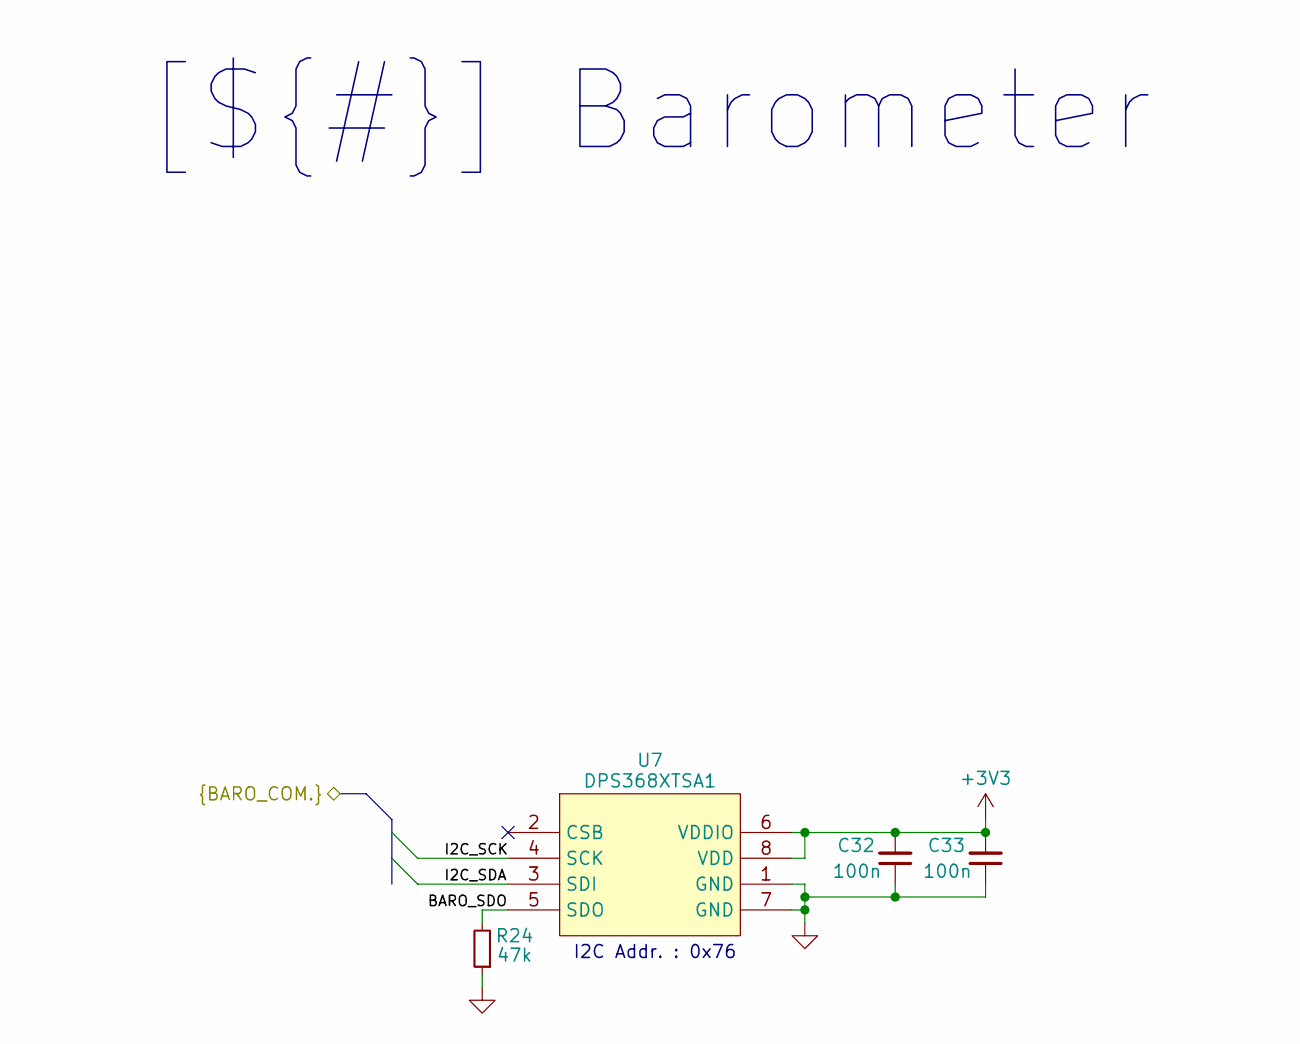
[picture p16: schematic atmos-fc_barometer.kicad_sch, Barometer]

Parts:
C32, C33: 100n; C_0402_1005Metric; Mfr Part Number MSASE105SB7104KFNA01
R24: 47k; R_0402_1005Metric; Mfr Part Number CRCW040247K0FKEDC
U7: DPS368XTSA1; Infineon_PG-VLGA-8-2; Mfr Part Number DPS368XTSA1

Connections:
+3V3: C32.2, C33.2, U7.6 (VDDIO), U7.8 (VDD); also elsewhere on the board
/Barometer/BARO_SDO: R24.2, U7.5 (SDO)
/Connectors/I2C_SCK: U7.4 (SCK); also elsewhere on the board
/Connectors/I2C_SDA: U7.3 (SDI); also elsewhere on the board
GND: C32.1, C33.1, R24.1, U7.1 (GND), U7.7 (GND); also elsewhere on the board

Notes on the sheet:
[${#}] ${TITLE}
I2C Addr. : 0x76

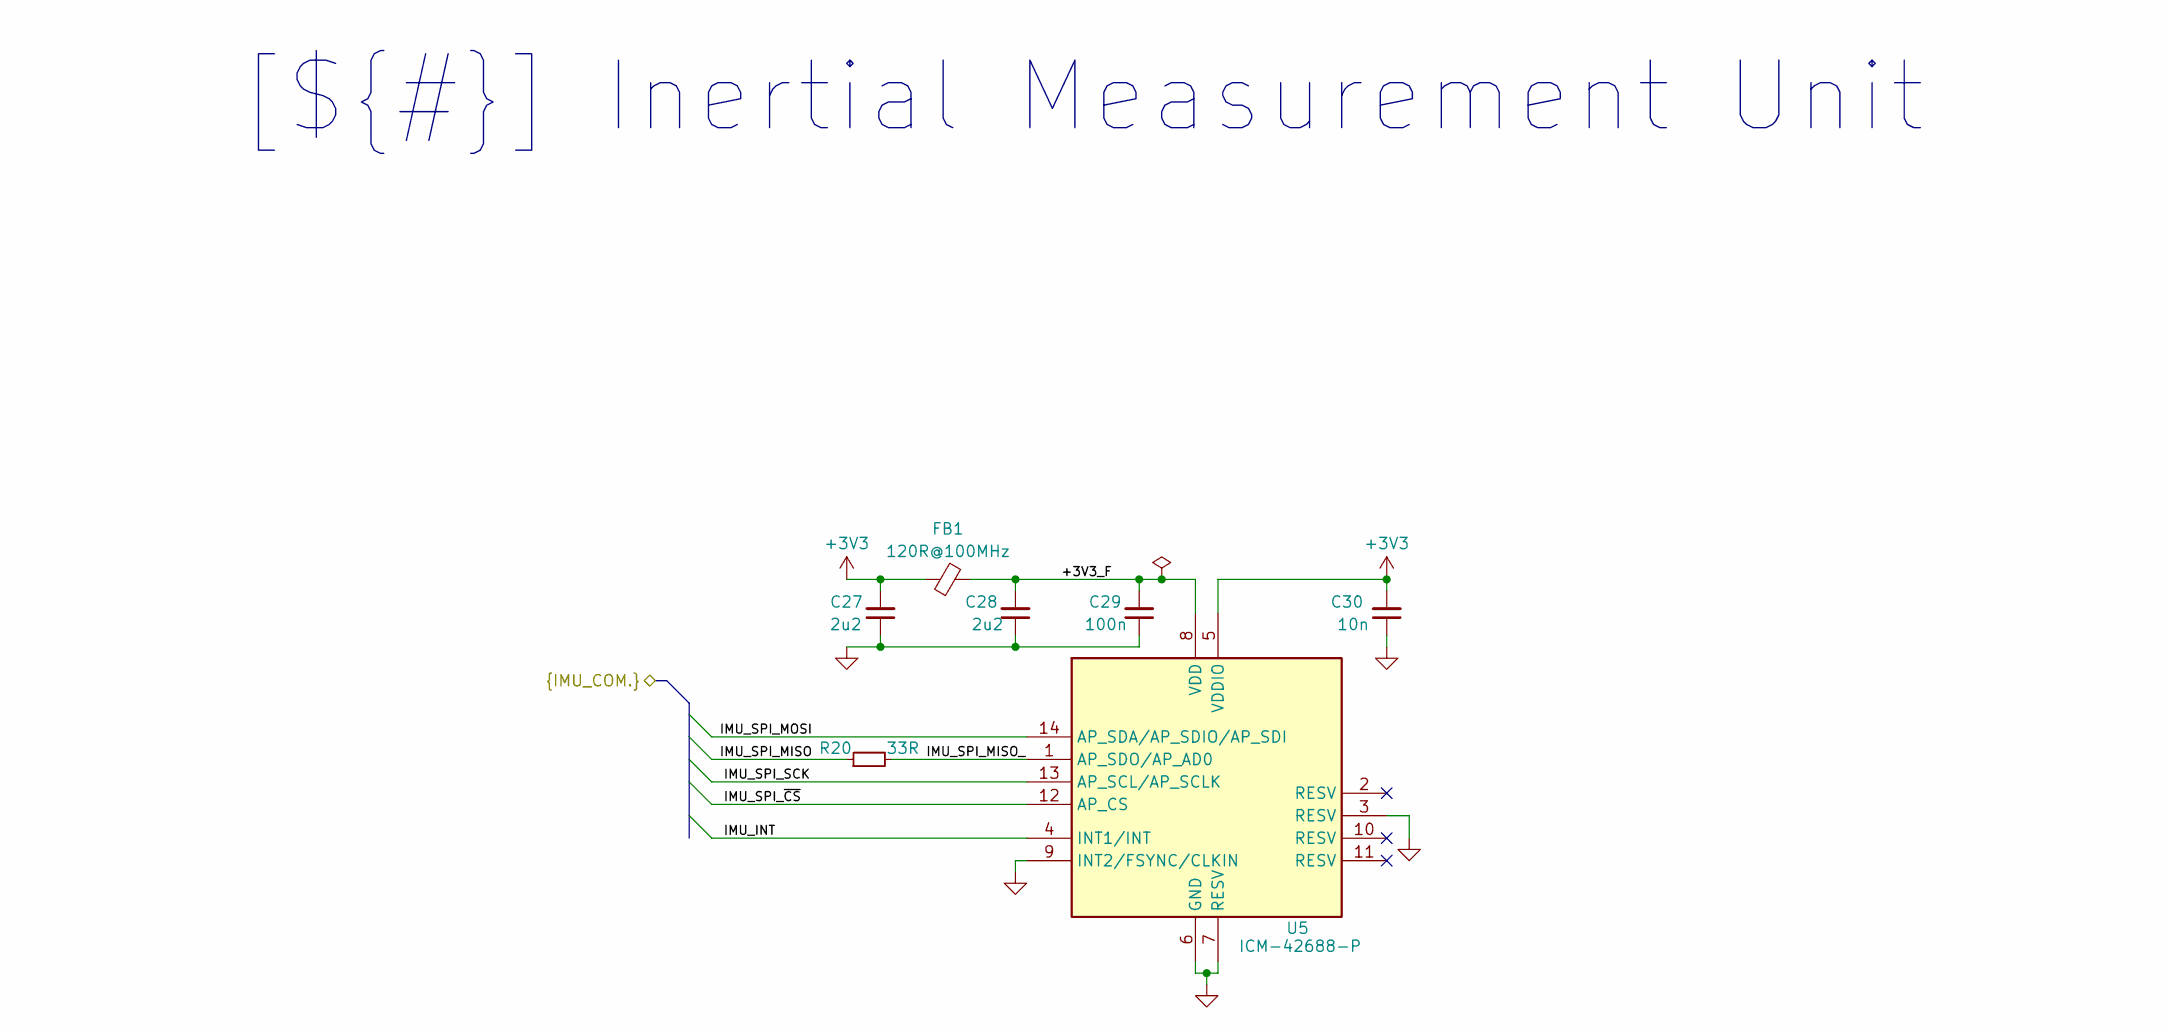
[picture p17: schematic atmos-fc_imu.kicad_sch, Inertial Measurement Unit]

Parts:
C27, C28: 2u2; C_0402_1005Metric; Mfr Part Number GRM155C71A225KE11D
C29: 100n; C_0402_1005Metric; Mfr Part Number MSASE105SB7104KFNA01
C30: 10n; C_0402_1005Metric; Mfr Part Number GRM1555C1E103GE01D
FB1: 120R@100MHz; L_0402_1005Metric; Mfr Part Number BLM15PX121BH1D
R20: 33R; R_0402_1005Metric; Mfr Part Number CRCW040220K0FKED
U5: ICM-42688-P; Mfr Part Number ICM-42688-P

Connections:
+3V3: C27.2, C30.2, FB1.1, U5.5 (VDDIO); also elsewhere on the board
/IMU/+3V3_F: C28.2, C29.2, FB1.2, U5.8 (VDD)
/IMU/IMU_INT: U5.4 (INT1/INT); also elsewhere on the board
/IMU/IMU_SPI_MISO: R20.1; also elsewhere on the board
/IMU/IMU_SPI_MISO_: R20.2, U5.1 (AP_SDO/AP_AD0)
/IMU/IMU_SPI_MOSI: U5.14 (AP_SDA/AP_SDIO/AP_SDI); also elsewhere on the board
/IMU/IMU_SPI_SCK: U5.13 (AP_SCL/AP_SCLK); also elsewhere on the board
/IMU/IMU_SPI_~CS: U5.12 (AP_CS); also elsewhere on the board
GND: C27.1, C28.1, C29.1, C30.1, U5.3 (RESV), U5.6 (GND), U5.7 (RESV), U5.9 (INT2/FSYNC/CLKIN); also elsewhere on the board

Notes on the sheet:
[${#}] ${TITLE}

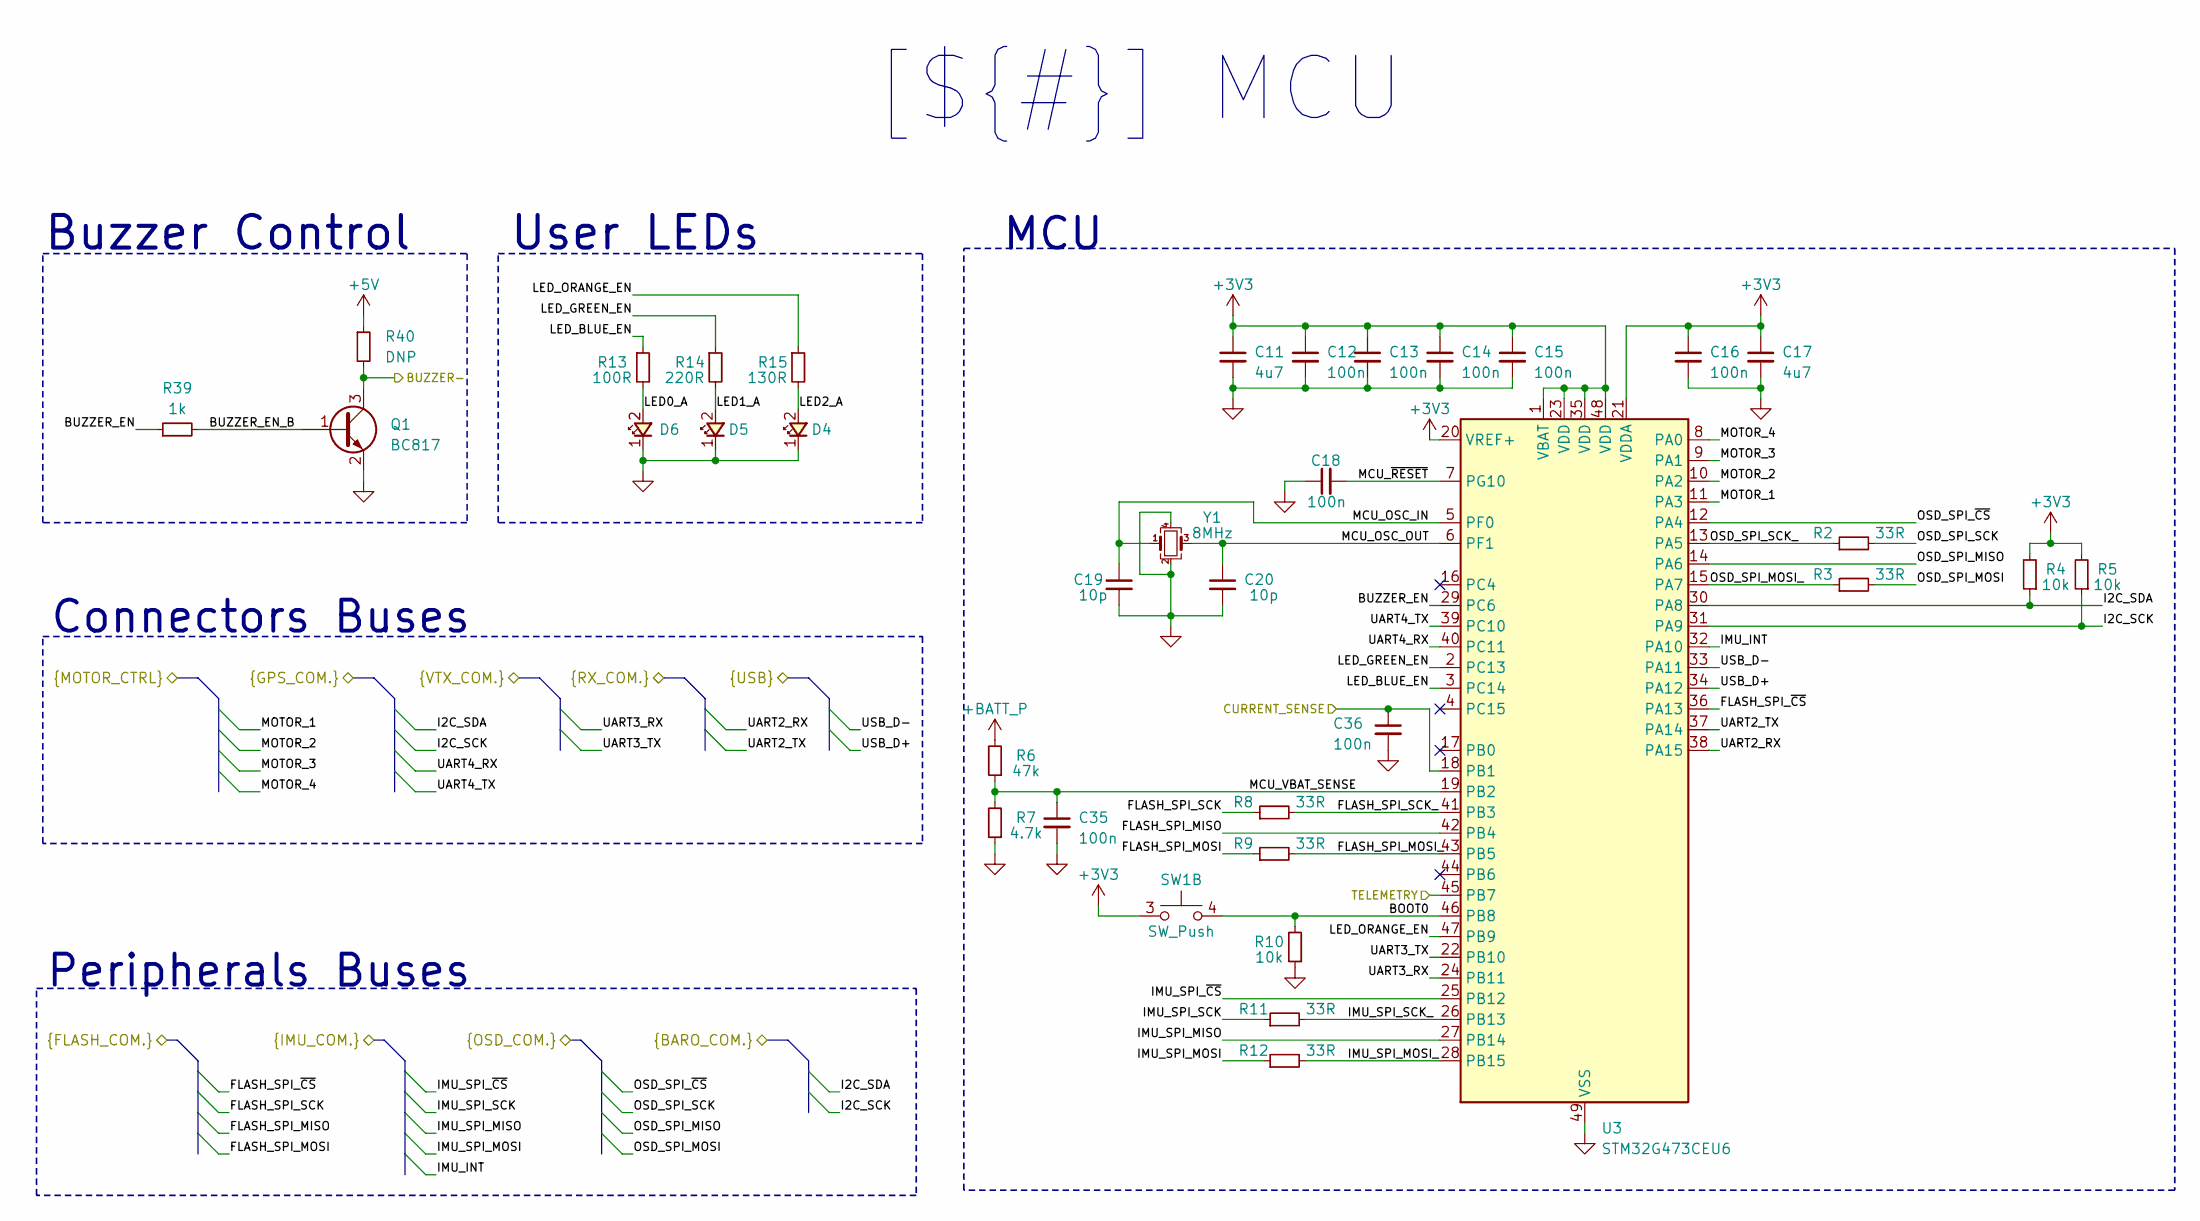
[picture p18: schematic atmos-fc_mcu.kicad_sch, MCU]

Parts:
C11, C17: 4u7; C_0603_1608Metric; Mfr Part Number GRM188Z71C475KE21J
C12, C13, C14, C15, C16, C18, C35, C36: 100n; C_0402_1005Metric; Mfr Part Number MSASE105SB7104KFNA01
C19, C20: 10p; C_0402_1005Metric; Mfr Part Number GRM1555C1H100JA01D
D4: LED_0603_1608Metric; Mfr Part Number LO Q976-PS-25
D5: LED_0603_1608Metric; Mfr Part Number LT Q39G-Q1OO-25-1
D6: LED_0603_1608Metric; Mfr Part Number LB Q39G-N1OO-35-1
Q1: BC817; DFN1010D-3; Mfr Part Number BC817-40QBH-QZ
R2, R3, R8, R9, R11, R12: 33R; R_0402_1005Metric; Mfr Part Number CRCW040220K0FKED
R4, R5, R10: 10k; R_0402_1005Metric; Mfr Part Number CRCW040210K0FKEDC
R6: 47k; R_0402_1005Metric; Mfr Part Number CRCW040247K0FKEDC
R7: 4.7k; R_0402_1005Metric; Mfr Part Number CRCW04024K70FKEDC
R13: 100R; R_0402_1005Metric; Mfr Part Number CRCW0402100RFKEDC
R14: 220R; R_0402_1005Metric; Mfr Part Number CRCW0402220RFKED
R15: 130R; R_0402_1005Metric; Mfr Part Number CRCW0402130RFKEDC
R39: 1k; R_0402_1005Metric; Mfr Part Number CRCW04021K00FKED
R40: DNP; R_0402_1005Metric
SW1: SW_Push; Wurth_436331045822; Mfr Part Number 436331045822
U3: STM32G473CEU6; QFN-48-1EP_7x7mm_P0.5mm_EP5.6x5.6mm; Mfr Part Number STM32G473CEU6
Y1: 8MHz; Crystal_SMD_ECS_ECX33_4Pin_3.2x2.5mm; Mfr Part Number ECS-80-10-33-CGN-TR3

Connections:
+3V3: C11.1, C12.1, C13.1, C14.1, C15.1, C16.1, C17.1, R4.2, R5.2, SW1.3 (C), U3.1 (VBAT), U3.20 (VREF+), U3.21 (VDDA), U3.23 (VDD), U3.35 (VDD), U3.48 (VDD); also elsewhere on the board
+5V: R40.1; also elsewhere on the board
+BATT_P: R6.2; also elsewhere on the board
/Connectors/BUZZER-: Q1.3 (C), R40.2; also elsewhere on the board
/Connectors/CURRENT_SENSE: C36.1, U3.18 (PB1); also elsewhere on the board
/Connectors/I2C_SCK: R5.1, U3.31 (PA9); also elsewhere on the board
/Connectors/I2C_SDA: R4.1, U3.30 (PA8); also elsewhere on the board
/Connectors/MOTOR_1: U3.11 (PA3); also elsewhere on the board
/Connectors/MOTOR_2: U3.10 (PA2); also elsewhere on the board
/Connectors/MOTOR_3: U3.9 (PA1); also elsewhere on the board
/Connectors/MOTOR_4: U3.8 (PA0); also elsewhere on the board
/Connectors/TELEMETRY: U3.45 (PB7); also elsewhere on the board
/Connectors/UART2_RX: U3.38 (PA15); also elsewhere on the board
/Connectors/UART2_TX: U3.37 (PA14); also elsewhere on the board
/Connectors/UART3_RX: U3.24 (PB11); also elsewhere on the board
/Connectors/UART3_TX: U3.22 (PB10); also elsewhere on the board
/Connectors/UART4_RX: U3.40 (PC11); also elsewhere on the board
/Connectors/UART4_TX: U3.39 (PC10); also elsewhere on the board
/Connectors/USB_D+: U3.34 (PA12); also elsewhere on the board
/Connectors/USB_D-: U3.33 (PA11); also elsewhere on the board
/Flash Memory/FLASH_SPI_MISO: U3.42 (PB4); also elsewhere on the board
/Flash Memory/FLASH_SPI_MOSI: R9.1; also elsewhere on the board
/Flash Memory/FLASH_SPI_SCK: R8.1; also elsewhere on the board
/Flash Memory/FLASH_SPI_~CS: U3.36 (PA13); also elsewhere on the board
/IMU/IMU_INT: U3.32 (PA10); also elsewhere on the board
/IMU/IMU_SPI_MISO: U3.27 (PB14); also elsewhere on the board
/IMU/IMU_SPI_MOSI: R12.1; also elsewhere on the board
/IMU/IMU_SPI_SCK: R11.1; also elsewhere on the board
/IMU/IMU_SPI_~CS: U3.25 (PB12); also elsewhere on the board
/MCU/BOOT0: R10.2, SW1.4 (D), U3.46 (PB8)
/MCU/BUZZER_EN: R39.1, U3.29 (PC6)
/MCU/BUZZER_EN_B: Q1.1 (B), R39.2
/MCU/FLASH_SPI_MOSI_: R9.2, U3.43 (PB5)
/MCU/FLASH_SPI_SCK_: R8.2, U3.41 (PB3)
/MCU/IMU_SPI_MOSI_: R12.2, U3.28 (PB15)
/MCU/IMU_SPI_SCK_: R11.2, U3.26 (PB13)
/MCU/LED0_A: D6.2, R13.2
/MCU/LED1_A: D5.2, R14.2
/MCU/LED2_A: D4.2, R15.2
/MCU/LED_BLUE_EN: R13.1, U3.3 (PC14)
/MCU/LED_GREEN_EN: R14.1, U3.2 (PC13)
/MCU/LED_ORANGE_EN: R15.1, U3.47 (PB9)
/MCU/MCU_OSC_IN: C19.1, U3.5 (PF0), Y1.1
/MCU/MCU_OSC_OUT: C20.1, U3.6 (PF1), Y1.3
/MCU/MCU_VBAT_SENSE: C35.1, R6.1, R7.2, U3.19 (PB2)
/MCU/MCU_~RESET: C18.2, U3.7 (PG10)
/MCU/OSD_SPI_MISO: U3.14 (PA6); also elsewhere on the board
/MCU/OSD_SPI_MOSI: R3.2; also elsewhere on the board
/MCU/OSD_SPI_MOSI_: R3.1, U3.15 (PA7)
/MCU/OSD_SPI_SCK: R2.2; also elsewhere on the board
/MCU/OSD_SPI_SCK_: R2.1, U3.13 (PA5)
/MCU/OSD_SPI_~CS: U3.12 (PA4); also elsewhere on the board
GND: C11.2, C12.2, C13.2, C14.2, C15.2, C16.2, C17.2, C18.1, C19.2, C20.2, C35.2, C36.2, D4.1, D5.1, D6.1, Q1.2 (E), R7.1, R10.1, U3.49 (VSS), Y1.2, Y1.4; also elsewhere on the board

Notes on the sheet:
[${#}] ${TITLE}
MCU
Peripherals Buses
Buzzer Control
Connectors Buses
User LEDs

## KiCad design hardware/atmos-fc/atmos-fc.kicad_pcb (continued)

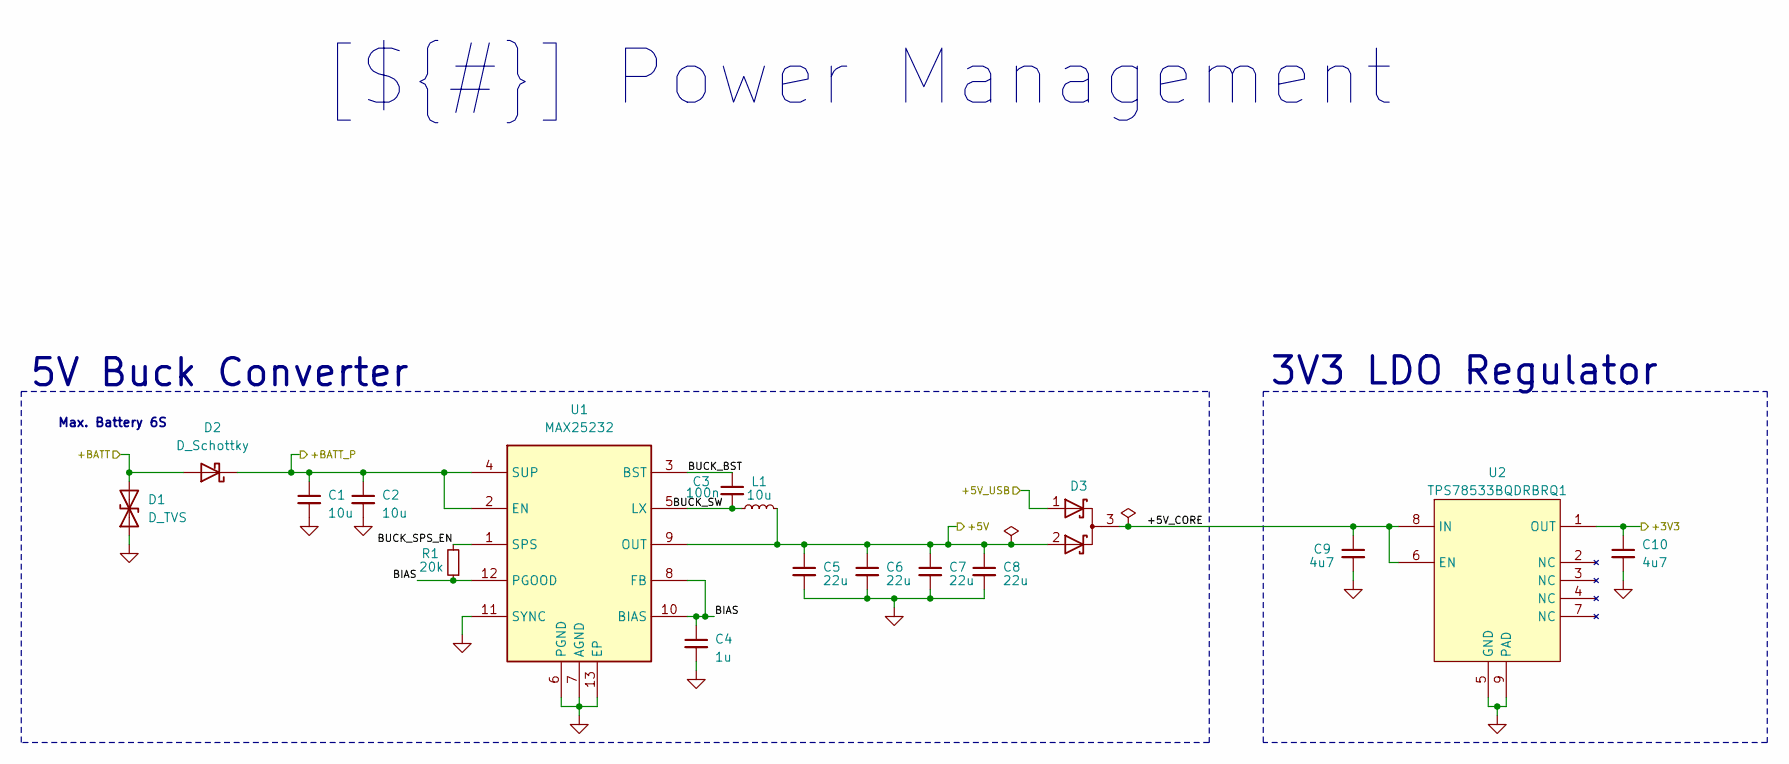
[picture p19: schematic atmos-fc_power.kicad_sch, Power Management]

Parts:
C1, C2: 10u; C_1206_3216Metric; Mfr Part Number MCJCG31LBB7106KTPA01
C3: 100n; C_0402_1005Metric; Mfr Part Number MSASE105SB7104KFNA01
C4: 1u; C_0603_1608Metric; Mfr Part Number MSAST168SB7105KTNA01
C5, C6, C7, C8: 22u; C_1206_3216Metric; Mfr Part Number MSASE31LBB7226MTNA01
C9, C10: 4u7; C_0603_1608Metric; Mfr Part Number GRM188Z71C475KE21J
D1: D_TVS; D_SOD-882; Mfr Part Number PESD30VF1BBL-QYL
D2: D_Schottky; DFN3820A; Mfr Part Number V7N103HM3/I
D3: PMEG2020CPASX; HUSON-3-1EP_2x2mm_P1.3mm_EP1.1x1.6mm; Mfr Part Number PMEG2020CPASX
L1: 10u; L_Bourns_SRP5030CC; Mfr Part Number SRP5030CC-100M
R1: 20k; R_0402_1005Metric; Mfr Part Number CRCW040220K0FKED
U1: MAX25232; Maxim_TDFN-12-1EP_3x3mm_P0.5mm_EP1.7x2.5mm_ThermalVias; Mfr Part Number MAX25232ATCD_V+
U2: TPS78533BQDRBRQ1; VSON-8-1EP_3x3mm_P0.65mm_EP1.65x2.4mm_ThermalVias; Mfr Part Number TPS78533BQWDRBRQ1

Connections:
+3V3: C10.1, U2.1 (OUT); also elsewhere on the board
+5V: C5.1, C6.1, C7.1, C8.1, D3.2 (K), L1.2, U1.9 (OUT); also elsewhere on the board
+BATT_P: C1.1, C2.1, D2.1 (K), U1.2 (EN), U1.4 (SUP); also elsewhere on the board
/Connectors/+5V_USB: D3.1 (K); also elsewhere on the board
/Connectors/+BATT: D1.2 (A2), D2.2 (A); also elsewhere on the board
/Power Management/+5V_CORE: C9.1, D3.3 (A), U2.6 (EN), U2.8 (IN)
/Power Management/BIAS: C4.1, R1.1, U1.8 (FB), U1.10 (BIAS), U1.12 (PGOOD)
/Power Management/BUCK_BST: C3.1, U1.3 (BST)
/Power Management/BUCK_SPS_EN: R1.2, U1.1 (SPS)
/Power Management/BUCK_SW: C3.2, L1.1, U1.5 (LX)
GND: C1.2, C2.2, C4.2, C5.2, C6.2, C7.2, C8.2, C9.2, C10.2, D1.1 (A1), U1.6 (PGND), U1.7 (AGND), U1.11 (SYNC), U1.13 (EP), U2.5 (GND), U2.9 (PAD); also elsewhere on the board

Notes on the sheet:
[${#}] ${TITLE}
5V Buck Converter
3V3 LDO Regulator
Max. Battery 6S

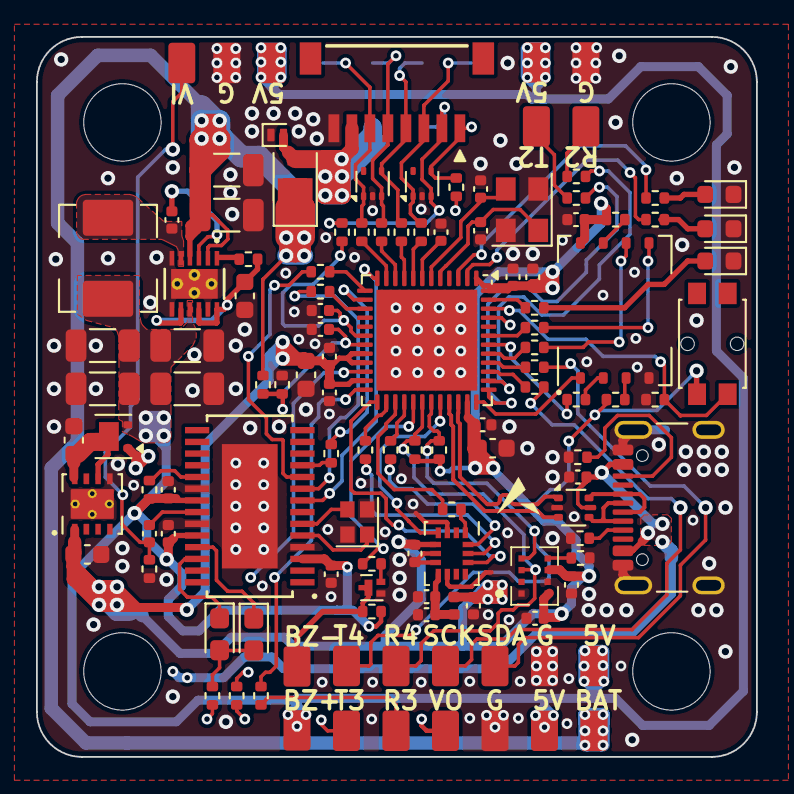
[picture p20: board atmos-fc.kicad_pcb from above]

Board: 4 copper layers, 40.0 x 40.0 mm, 110 parts (1 on the bottom side), 90 nets.

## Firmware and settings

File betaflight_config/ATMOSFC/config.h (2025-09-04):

/*
 * This file is part of Betaflight.
 *
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
 * See the GNU General Public License for more details.
 *
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
 * If not, see <http://www.gnu.org/licenses/>.
 */

#pragma once

#define FC_TARGET_MCU                   STM32G47X

#define BOARD_NAME                      ATMOSFC
#define MANUFACTURER_ID                 CUST

// IMU 
#define USE_ACC
#define USE_ACC_SPI_ICM42688P
#define USE_GYRO
#define USE_GYRO_SPI_ICM42688P

// BARO
#define USE_BARO
#define USE_BARO_DPS310

// BLACKBOX
#define USE_FLASH
#define USE_FLASH_W25Q128FV

// OSD
#define USE_MAX7456

// GPS + MAG 
#define USE_MAG
#define USE_GPS
#define USE_GPS_NMEA
#define USE_GPS_UBLOX
#define USE_GPS_RESCUE

// PINOUT
#define BEEPER_PIN                      PC6

#define MOTOR1_PIN                      PA3
#define MOTOR2_PIN                      PA2
#define MOTOR3_PIN                      PA1
#define MOTOR4_PIN                      PA0

#define UART1_TX_PIN                    PB6
#define UART1_RX_PIN                    PB7

#define UART2_TX_PIN                    PA14
#define UART2_RX_PIN                    PA15

#define UART3_TX_PIN                    PB10
#define UART3_RX_PIN                    PB11

#define UART4_TX_PIN                    PC10
#define UART4_RX_PIN                    PC11

#define I2C2_SCL_PIN                    PA9
#define I2C2_SDA_PIN                    PA8

#define SPI1_SCK_PIN                    PA5
#define SPI1_SDI_PIN                    PA6
#define SPI1_SDO_PIN                    PA7

#define SPI2_SCK_PIN                    PB13
#define SPI2_SDI_PIN                    PB14
#define SPI2_SDO_PIN                    PB15

#define SPI3_SCK_PIN                    PB3
#define SPI3_SDI_PIN                    PB4
#define SPI3_SDO_PIN                    PB5

#define MAX7456_SPI_CS_PIN              PA4
#define GYRO_1_CS_PIN                   PB12
#define GYRO_1_EXTI_PIN                 PA10
#define FLASH_CS_PIN                    PA13

#define ADC_VBAT_PIN                    PB2
#define ADC_CURR_PIN                    PB1

#define LED0_PIN                        PC14
#define LED1_PIN                        PC13
#define LED2_PIN                        PB9

// TIMER
#define TIMER_PIN_MAPPING \
        TIMER_PIN_MAP( 0, MOTOR1_PIN , 2,  1) \
        TIMER_PIN_MAP( 1, MOTOR2_PIN , 2,  2) \
        TIMER_PIN_MAP( 2, MOTOR3_PIN , 1,  3) \
        TIMER_PIN_MAP( 3, MOTOR4_PIN , 1,  4) \
        TIMER_PIN_MAP( 4, BEEPER_PIN , 2,  5) \

// DMA
#define SPI1_RX_DMA_OPT              6
#define SPI1_TX_DMA_OPT              7
#define SPI2_RX_DMA_OPT              8
#define SPI2_TX_DMA_OPT              9
#define SPI3_RX_DMA_OPT              10
#define SPI3_TX_DMA_OPT              11
#define ADC1_DMA_OPT                 12
#define ADC2_DMA_OPT                 13

// DEVICE BUS
#define MAX7456_SPI_INSTANCE         SPI1
#define GYRO_1_SPI_INSTANCE          SPI2
#define FLASH_SPI_INSTANCE           SPI3
#define BARO_I2C_INSTANCE            (I2CDEV_2)
#define MAG_I2C_INSTANCE             (I2CDEV_2)

// CONFIG
#define BEEPER_INVERTED
#define DEFAULT_BLACKBOX_DEVICE      BLACKBOX_DEVICE_FLASH
#define DEFAULT_CURRENT_METER_SOURCE CURRENT_METER_ADC
#define DEFAULT_VOLTAGE_METER_SOURCE VOLTAGE_METER_ADC
#define DEFAULT_VOLTAGE_METER_SCALE  110
#define DEFAULT_DSHOT_BURST 	     DSHOT_DMAR_ON
#define GYRO_1_ALIGN                 CW180_DEG
#define ICM426XX_CLOCK 		     10000000 

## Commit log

2025-09-02 Add sources files
    [atmos-fc-B_Cu.gbr, atmos-fc-B_Mask.gbr, atmos-fc-B_Paste.gbr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]
2025-09-03 Improved layout
    Added oversized holes for mounting silicone inserts and improved layout.
    [atmos-fc.kicad_pcb, atmos-fc_connectors.kicad_sch]
2025-09-03 Add GYRO_1_EXTI Pin
    [atmos-fc.kicad_pcb, atmos-fc_imu.kicad_sch, atmos-fc_mcu.kicad_sch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]
2025-09-03 Add soldering pads for ESC
    [atmos-fc.kicad_pcb, atmos-fc_connectors.kicad_sch, atmos-fc_mcu.kicad_sch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]
2025-09-04 Added 100n on ADC inputs and improved layout
    [atmos-fc.kicad_pcb, atmos-fc_connectors.kicad_sch, atmos-fc_mcu.kicad_sch]
2025-09-04 Update schematic

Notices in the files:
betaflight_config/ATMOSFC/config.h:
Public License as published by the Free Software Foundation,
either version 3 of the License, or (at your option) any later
